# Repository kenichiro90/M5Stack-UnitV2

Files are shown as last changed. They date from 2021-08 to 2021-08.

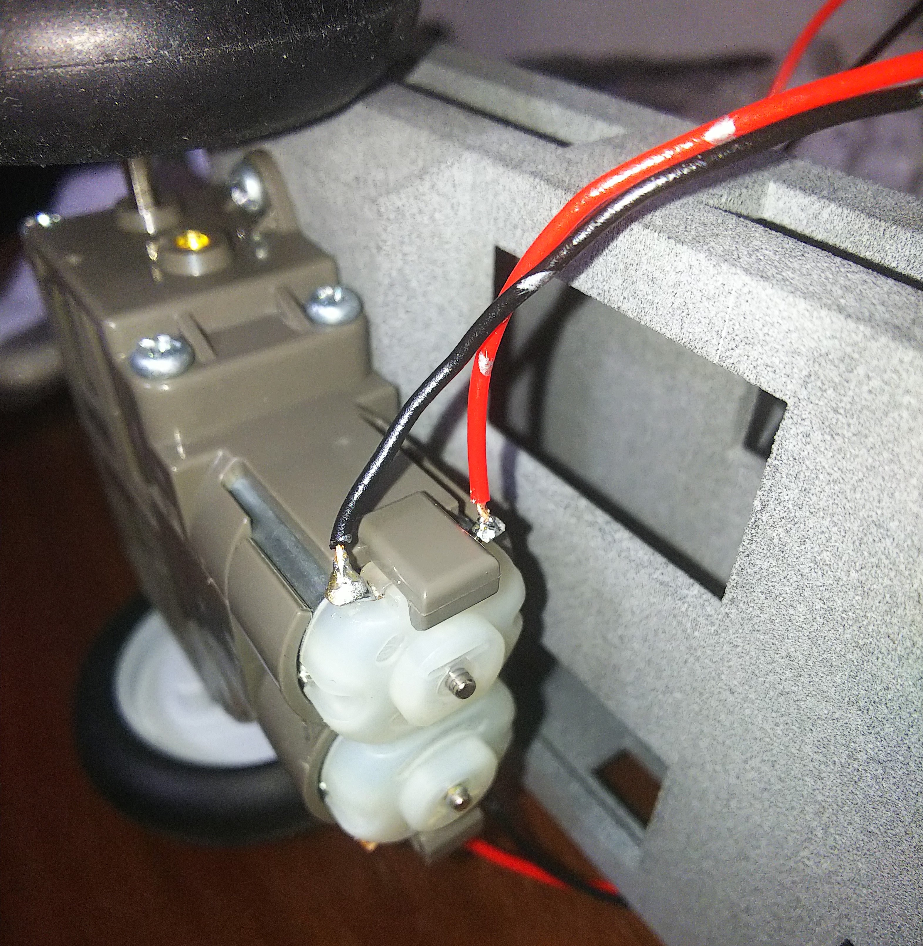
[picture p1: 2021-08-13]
Picture_2.jpg

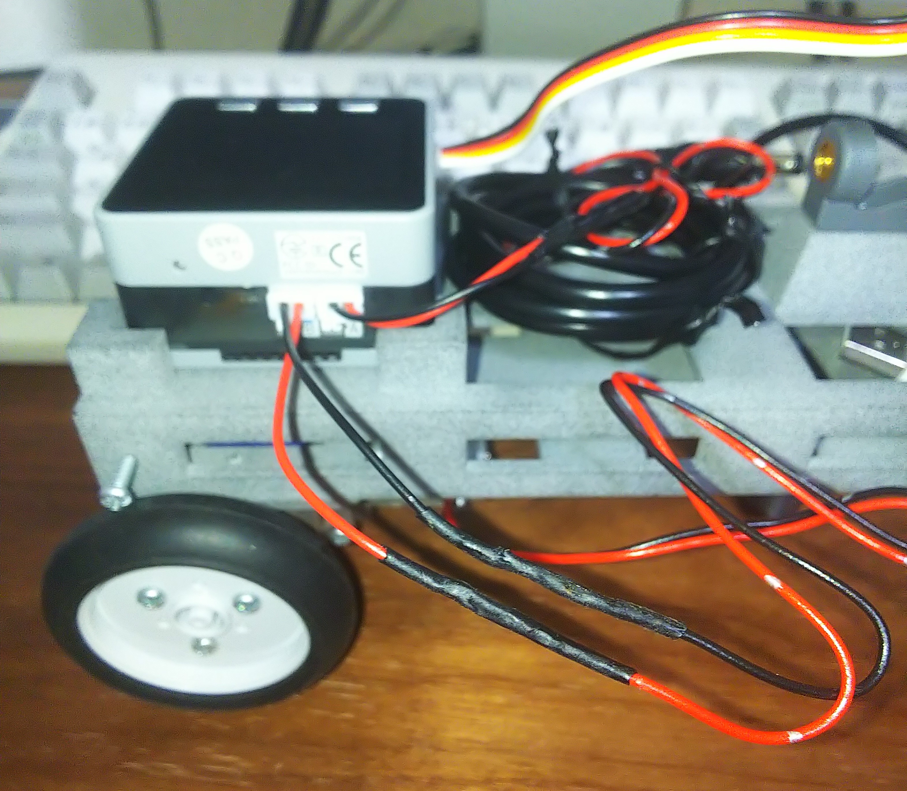
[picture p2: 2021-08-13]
Picture_1.jpg

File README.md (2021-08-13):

# README

## 注意点

モーターとGOPLUS2モジュールとの接続には、GOPLUS2モジュール付属の配線材を使用する。

前記配線材の長さは極めて短いため、そのままの状態ではモーターとの接続ができない。

そのため、下記手順により前記配線材の延長を行う。

### 配線材(GOPLUS2モジュール付属)の延長手順

1. GOPLUS2モジュール付属の配線材の先端を、ニッパー等で切り落とす。
2. ワイヤーストリッパーを用い、切り落とした端面から10mm程度、配線材の被覆を剥く。
3. 導体断面積:0.2~0.3sq, 長さ:30cm程度の配線材を4本用意し、2.と同様にして配線材の被覆を剥く。
4. 2.と3.で用意した配線材を撚り合わせる。
5. 撚り合わせた部分に、任意量のハンダを巻きつける。
6. ハンダこてを用い、巻きつけたハンダを溶かすことで、配線材の延長を行う。
7. ハンダが露出している長さ程度の熱収縮チューブを用意し、延長部に被せる。
8. ハンダこてを用い、熱収縮チューブを収縮させる。
9. テスターを用い、配線材(延長後)の導通確認を行う。

延長後、配線材の先端とモーターの端子部とをはんだ付けすることで、接点を取る。

-----

## 部品表

| No.  | 品名 | 購入先 | 単価 | 数量 | 価格 |
| ---- | --- | --- | --- | ---- | --- |
| 1 | [Anker PowerCore Slim 10000 PD 20W (10000mAh PD モバイルバッテリー 超大容量)【USB Power Delivery対応/PowerIQ搭載/PSE技術基準適合】 iPhone 12 iPad Air(第4世代) Android その他 各種機器対応](https://www.amazon.co.jp/gp/product/B08K31B6M2/ref=ppx_yo_dt_b_asin_title_o02_s00?ie=UTF8&psc=1) | Amazon | 3,990  | 1 | 3,990  |
| 2 | [タミヤ 楽しい工作シリーズ No.168 ダブルギヤボックス 左右独立4速タイプ (70168)](https://www.amazon.co.jp/gp/product/B001Q13BIU/ref=ppx_yo_dt_b_asin_title_o02_s00?ie=UTF8&psc=1) | Amazon | 653 | 1 | 653 |
| 3 | [タミヤ 楽しい工作シリーズ No.145 ナロータイヤセット 58mm径 (70145)](https://www.amazon.co.jp/gp/product/B001VZJDZ6/ref=ppx_yo_dt_b_asin_title_o02_s00?ie=UTF8&psc=1) | Amazon | 385 | 1 | 385 |
| 4 | [タミヤ 楽しい工作シリーズ No.144 ボールキャスター 2セット入 (70144)](https://www.amazon.co.jp/gp/product/B001VZHRW2/ref=ppx_yo_dt_b_asin_title_o02_s00?ie=UTF8&psc=1) | Amazon | 268 | 1 | 268 |
| 5 | [USB電源ケーブル Type-C PDトリガーケーブル DC プラグ 外径5.5mm/内径2.1mm（2.5mm) (9V 3A)](https://www.amazon.co.jp/gp/product/B08DTCLXRN/ref=ppx_yo_dt_b_asin_title_o01_s00?ie=UTF8&psc=1) | Amazon | 1,380  | 1 | 1,380  |
| | | | 計 | | 6,676  |
| | | | | | |
| 6 | [M5Stack用GOPLUS2モジュール](https://www.switch-science.com/catalog/6736/) | スイッチサイエンス | 2,420  | 1 | 2,420  |
| 7 | [M5Stack Core2 for AWS - ESP32 IoT開発キット](https://www.switch-science.com/catalog/6784/) | スイッチサイエンス | 7,018  | 1 | 7,018  |
| 8 | [M5Stack UnitV2 AI カメラ（SSD202D）](https://www.switch-science.com/catalog/7160/) | スイッチサイエンス | 9,592  | 1 | 9,592  |
| 9 | [M5Stack用GROVE互換ケーブル 50 cm（2個入り）](https://www.switch-science.com/catalog/5215/) | スイッチサイエンス | 319 | 1 | 319 |
| | | | 計 | | 19,349 |
| | | | | | |
| 10 | [CAVS0.3SQ-2X6(A)](https://www.marutsu.co.jp/pc/i/2190499/)  | マルツオンライン | 724 | 1 | 724 |
| 11 | [【ｽﾐﾁｭｰﾌﾞC2B】熱収縮チューブ 低温収縮型 2mm 黒 1mカット品](https://www.marutsu.co.jp/pc/i/10002/) | マルツオンライン | 45 | 1 | 45 |
| | | | 計 | | 769 |
| | | | | | |
| 12 | カスタム品-1("シャシー.stl", PA12 ナチュラル(MJF)) | DMM.make | 12,646 | 1 | 12,646 |
| 13 | カスタム品-2("留め具.stl", PA12 ナチュラル(MJF)) | DMM.make | 1,930  | 1 | 1,930  |
| | | | 計 | | 14,576 |

-----

## 3Dモデル(組立て後)の説明

本モデルは、Autodesk Fusion 360にて作成した。

本モデルの状態を確認するには、"本体 v55.f3z"をAutodesk Fusion 360から開くこと。

本モデルには、3Dプリンタで出力するパーツ(カスタム品)の3Dモデルと、購入品の3Dモデルが含まれている。

各モデルの名称等は、下記の通り。

- 本体 v55.f3z
  - ボディ1(カスタム品, シャシー.stl)
  - コンポーネント1(カスタム品, 留め具.stl)
  - バッテリ(購入品, 部品表No.1)
  - モーター(購入品, 部品表No.2)
  - タイヤ(購入品, 部品表No.3)
  - ボールキャスター(購入品, 部品表No.4)
  - カメラ用マウント(購入品, 部品表No.8付属品)

-----

## 3Dプリンタで出力するパーツ

下記パーツを、DMM.makeで出力すること。

- "シャシー.stl" x 1個
- "留め具.stl" x 1個

出力時の材質は、"MJF, PA12 ナチュラル"とすること。

-----

## 各パーツ組付け時に使用するネジ

各パーツ組付け時に使用するネジは、部品表No.2, 部品表No.4付属のタッピングビスを使用する。

使用するタッピングビスは、3x12mmと3x8mmの2種類である。

3x8mmのタッピングビスは、部品表No.2のパーツをシャシーに対して固定するために使用する。

3x12mmのタッピングビスは、留め具をシャシーに対して固定するため、及び、部品表No.4のパーツをシャシーに対して固定するため、及び、部品表No.8付属のカメラ用マウント部品をシャシーに対して固定するために使用する。

-----

## モーター制御用ファームウェア("GOPLUS2.ino")

このファームウェアをM5Stackに書き込むと、GOPLUS2モジュールによるモーター制御が行えるようになる。

モーター制御を行うには、M5Stackとシリアル通信を確立する必要がある。

シリアル通信の設定条件は、下記の通り。

### シリアル通信の設定条件

- 受信用ポート(M5Stack, RX): 16番ピン
- 送信用ポート(M5Stack, TX): 17番ピン
- ボーレート: 115200bps
- データ長: 8bit
- パリティ: なし
- ストップビット: 1bit

モーター制御用コマンドは、下記の通り。なお、回転速度は、バイナリデータ(ASCII)で送信する必要があるため注意すること。

### モーター制御用コマンド

- 後退コマンド: "RWD\[SPD_MOT_0\]\[SPD_MOT_1\]\\n"
- 前進コマンド: "FWD\[SPD_MOT_0\]\[SPD_MOT_1\]\\n"
  - "\[SPD_MOT_0\], \[SPD_MOT_1\]"は、それぞれ1文字分のバイナリデータ(char)とする。
  - 文字データのエンコード形式は、"ASCII"とする。
  - "\[SPD_MOT_0\], \[SPD_MOT_1\]"で、モーターの回転速度を指定できる。
  - モーターの回転速度は"0~255"の範囲で指定できるが、上限値("60")を超えた場合、強制的に"60"に設定される。
- 停止コマンド: "STP\\n"

```pyserial```を使ったモーター制御の一例は、```motor_test.py```に記した通り。この例では、M5StackとUnitV2との間で、シリアル通信を確立している。接続の際は、GROVE互換ケーブルと[GROVE用 4ピン変換コネクタ（10個入り）](https://www.switch-science.com/catalog/7093/)、[普通のジャンパワイヤ（メス～メス）](https://www.switch-science.com/catalog/2295/)を使用した。

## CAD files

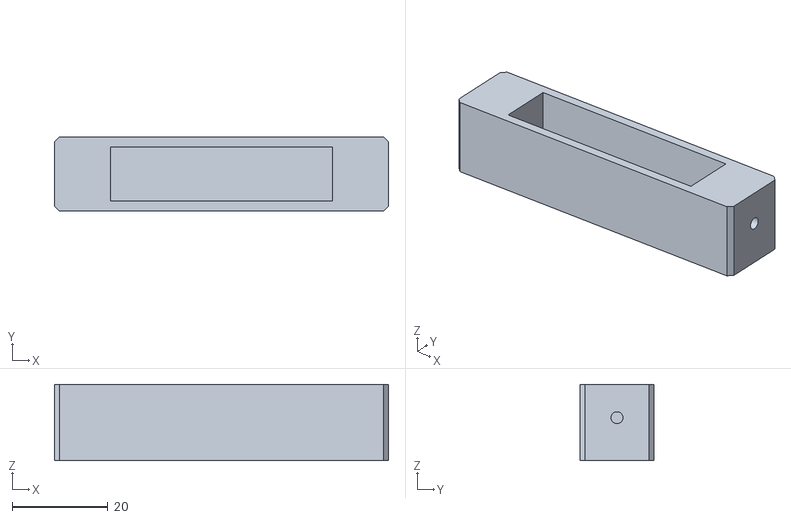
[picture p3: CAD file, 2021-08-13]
3Dモデルデータ/留め具.stl
69.9 x 15.4 x 16.0

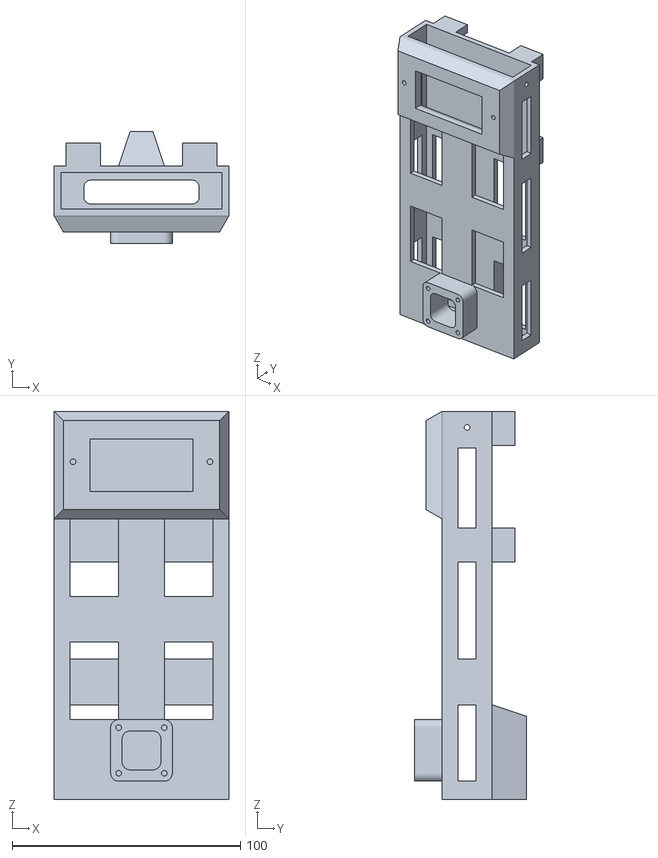
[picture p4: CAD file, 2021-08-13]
3Dモデルデータ/シャシー.stl
76.5 x 49.0 x 170.0

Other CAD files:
3Dモデルデータ/本体 v55.f3z

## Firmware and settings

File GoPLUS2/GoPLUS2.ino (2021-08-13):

/*
  Description: Use GoPLUS Module for four-channel servo test and three-channel ADC test.
*/
#include <M5Stack.h>
#include <Wire.h>
#include "GoPlus2.h"
#include <math.h>

// シリアル通信("M5Stack <-> M5UnitV2")で使用するポート番号の定義
#define rxPin 16
#define txPin 17

// クラスの初期化
GoPlus2 goPlus;


void header(const char *string, uint16_t color)
{
  // LCDにヘッダ文字を表示させる
  M5.Lcd.fillScreen(color);
  M5.Lcd.setTextSize(1);
  M5.Lcd.setTextColor(TFT_WHITE, TFT_BLACK);
  M5.Lcd.fillRect(0, 0, 320, 30, TFT_BLACK);
  M5.Lcd.setTextDatum(TC_DATUM);
  M5.Lcd.drawString(string, 160, 3, 4);
}

void Motor()
{
  // 変数の初期化
  unsigned char buf_speed = 0;
  short spd_mot_0 = 0;
  short spd_mot_1 = 0;

  while (1) {
    // デバイス状態の取得
    M5.update();

    // 受信バッファにデータが溜まっていた場合、1文字ずつ受信して配列に詰める
    if(Serial2.available() > 0) {
      byte data_size = Serial2.available();
      byte buf[data_size];
      for(byte i = 0; i < data_size; i++) {
        buf[i] = Serial2.read();
      }

      // 受信したデータを解析して、各コマンドを実行する
      if(buf[0] == 'R' && buf[1] == 'W' && buf[2] == 'D') {
        // -----
        // 後退コマンド: "RWD[SPD_MOT_0][SPD_MOT_1]"
        // -----
        //   "[SPD_MOT_0], [SPD_MOT_1]"は、1文字のデータ(char)とする。
        //   文字データのエンコード形式は、"ASCII"とする。
        //   "[SPD_MOT_0], [SPD_MOT_1]"で、モーターの回転速度を指定できる。
        //   モーターの回転速度は"0~255"の範囲で指定できるが、上限値("60")を超えた場合、強制的に"60"に設定される。
        // -----

        // 進行方向を表示する(シリアルポート)
        Serial.println("DIR: RWD");

        // モーターの回転速度の読み取り
        spd_mot_0 = buf[3];
        spd_mot_1 = buf[4];

        // 上限値("60")を超えた場合、回転速度を"60"に設定する
        if(spd_mot_0 > 60) spd_mot_0 = 60;
        if(spd_mot_1 > 60) spd_mot_1 = 60;

        // モーターの回転方向を変更する
        //spd_mot_0 = spd_mot_0;
        spd_mot_1 = spd_mot_1 * (-1);
 
        // モーターの回転速度を表示する(シリアルポート)
        Serial.println(spd_mot_0);
        Serial.println(spd_mot_1);

        // 進行方向とモーターの回転速度を表示する(LCD)
        M5.Lcd.fillRect(0, 40, 320, 100, TFT_BLACK);
        M5.Lcd.setCursor(20, 40, 4);
        M5.Lcd.println("Motor Direction: RWD");
        M5.Lcd.setCursor(20, 60, 4);
        M5.Lcd.print("Motor Speed: ");
        M5.Lcd.println(spd_mot_0);

        // モーターの回転を開始する
        goPlus.Motor_write_speed(MOTOR_NUM0, spd_mot_0);
        goPlus.Motor_write_speed(MOTOR_NUM1, spd_mot_1);
      } else if(buf[0] == 'F' && buf[1] == 'W' && buf[2] == 'D') {
        // -----
        // 前進コマンド: "FWD[SPD_MOT_0][SPD_MOT_1]"
        // -----
        //   "[SPD_MOT_0], [SPD_MOT_1]"は、1文字のデータ(char)とする。
        //   文字データのエンコード形式は、"ASCII"とする。
        //   "[SPD_MOT_0], [SPD_MOT_1]"で、モーターの回転速度を指定できる。
        //   モーターの回転速度は"0~255"の範囲で指定できるが、上限値("60")を超えた場合、強制的に"60"に設定される。
        // -----

        // 進行方向を表示する(シリアルポート)
        Serial.println("DIR: FWD");

        // モーターの回転速度の読み取り
        spd_mot_0 = buf[3];
        spd_mot_1 = buf[4];

        // 上限値("60")を超えた場合、回転速度を"60"に設定する
        if(spd_mot_0 > 60) spd_mot_0 = 60;
        if(spd_mot_1 > 60) spd_mot_1 = 60;

        // モーターの回転方向を変更する
        spd_mot_0 = spd_mot_0 * (-1);
        //spd_mot_1 = spd_mot_1;

        // モーターの回転速度を表示する(シリアルポート)
        Serial.println(spd_mot_0);
        Serial.println(spd_mot_1);

        // 進行方向とモーターの回転速度を表示する(LCD)
        M5.Lcd.fillRect(0, 40, 320, 100, TFT_BLACK);
        M5.Lcd.setCursor(20, 40, 4);
        M5.Lcd.println("Motor Direction: FWD");
        M5.Lcd.setCursor(20, 60, 4);
        M5.Lcd.print("Motor Speed: ");
        M5.Lcd.println(spd_mot_1);

        // モーターの回転を開始する
        goPlus.Motor_write_speed(MOTOR_NUM0, spd_mot_0);
        goPlus.Motor_write_speed(MOTOR_NUM1, spd_mot_1);
      } else if(buf[0] == 'S' && buf[1] == 'T' && buf[2] == 'P') {
        // -----
        // 停止コマンド: "STP"
        // -----
        //   文字データのエンコード形式は、"ASCII"とする。
        // -----

        // 進行方向を表示する(シリアルポート)
        Serial.println("DIR: STP");

        // 進行方向とモーターの回転速度を表示する(LCD)
        M5.Lcd.fillRect(0, 40, 320, 100, TFT_BLACK);
        M5.Lcd.setCursor(20, 40, 4);
        M5.Lcd.println("Motor Direction: STP");
        M5.Lcd.setCursor(20, 60, 4);
        M5.Lcd.println("Motor Speed: 0");

        // モーターの回転を停止する
        goPlus.Motor_write_speed(MOTOR_NUM0, 0);
        goPlus.Motor_write_speed(MOTOR_NUM1, 0);
      }
    }

    // 10msec毎に、受信バッファの確認と受信データの解析を実行する
    delay(10);
  }
}

void setup()
{
  // デバイスの初期化(M5Stack)
  M5.begin();

  // シリアル通信の開始
  Serial.begin(115200);                                                 // デバッグ用
  Serial2.begin(115200, SERIAL_8N1, rxPin, txPin);                      // "M5Stack <-> M5UnitV2"用

  // デバイスの初期化(GOPLUS2モジュール)
  goPlus.begin();

  // 少し待つ(100msec)
  delay(100);

  // LCDにヘッダ文字を表示させる
  header("GoPlus 2", TFT_BLACK);
  M5.Lcd.setTextColor(TFT_GREEN, TFT_BLACK);
}

void loop()
{
  // モーター制御の実行
  Motor();
}
